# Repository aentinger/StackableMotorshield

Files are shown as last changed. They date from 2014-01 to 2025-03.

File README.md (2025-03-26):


💾 Stackable Motorshield
========================



# 📸 Image

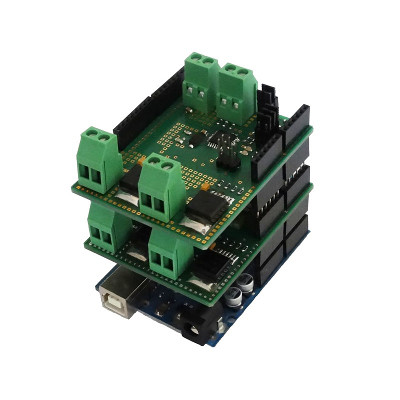
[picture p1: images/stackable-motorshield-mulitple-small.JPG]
LXRobotics P2 StackableMotorshield


# 📂 Description

The Stackable Motorshield facilitates the control of up to 8 high power motors (18 V / 46 A) using only one Arduino Board. This can be achived by using the same amount of Stackable Motorshields as the amount of motors desired to be controlled. The communication between Motorshields and Arduino Board is done over the I2C-Interface. The address of each Stackable Motorshields can be configured. Inputs for connecting rotary encoders for determining the number of rotations of the motor are available on the shield. For a quick and easy start, a open source Arduino library with sample programs is available.

**Features**

* Control of up to 8 High Power Motors through stacking of up to 8 Stackable Motorshields on top of each other
* Voltage supply range: 7 to 18 Volts
* Can be used with 2S, 3S and 4S LiPo-battery
* High performance: Maximum continuous output 46 A
* Control via I2C -  only 2 Arduino-Pins are required (SDA = A4, SCL = A5)
* I2C-PullUp-resistors connectable through jumper
* Adjustable address through jumper
* Inputs for rotary encoders
* Motor drivers are protected against short circuit (to ground/supply), overheating, overvoltage and undervoltage
* Arduino Library with example programs is available on GitHub
* 2 Status-LEDs (Orange: User LED, Red: Active when speed of motor > 0)

# 🎥 [Video](images/stackable_motorshield_demo.mp4)

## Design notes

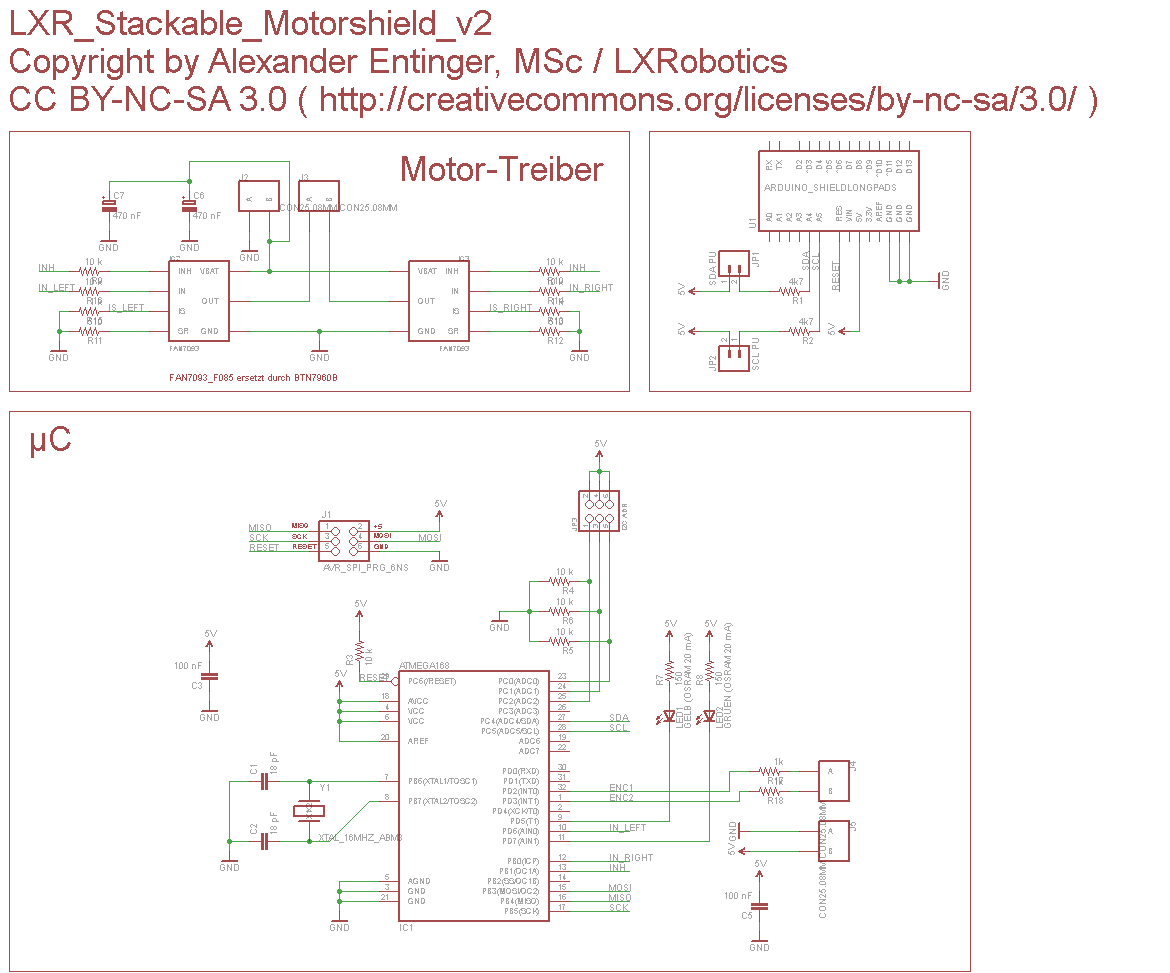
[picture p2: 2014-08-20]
hardware/lxr_stackable_motorshield_v2.png

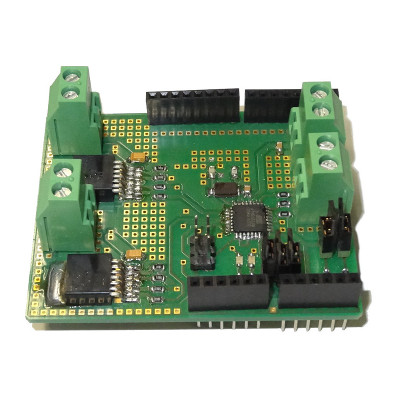
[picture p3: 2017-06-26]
images/stackable-motorshield-side-small.JPG

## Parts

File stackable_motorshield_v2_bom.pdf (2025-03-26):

Menge | Schaltplan | Bezeichnung | Farnell Bestell Nummer | Preis (1 Stück) | Gesamtpreis | Wird bestückt | Footprint | Säckchen
4 | J2, J3, J4, J5 | Schraubklemme 2 Polig | 3041165 | € 1,12 | € 4,48 | | | S1
2 | IC2, IC3 | FAN7093 Leistungshalbbrücke | 2290282 | € | 6,99 | € | 13,98 | x | Bei Farnell aus dem Sortiment genommen, Ersatztyp ist BTN7960B, Digikey-Bauteil-Bezeichnung BTN7960BCT-ND
2 | C6, C7 | KEMET Bauform A, 25 V, 470 nF, Tantal Ko | 1457425 | € | 0,15 | € | 0,30 | x | http://www.digikey.at/product-detail/de/BTN7960B/BTN7960BCT-ND/2231075
2 | C3, C5 | 100 nF, 100 V, 0805, Keramikkondensator | 1759144 | € 0,01 | € 0,02 | x
2 | C1, C2 | 18 pF, 100 V, 0805, Keramikkondensator | 1759194 | € 0,01 | € 0,03 | x
1 | Y1 | Quarz, 16 MHz, SMD | 1611806 | € 1,74 | € 1,74 | x
2 | R1, R2 | 4k7, 0805, Widerstand SMD | 1469923 | € 0,02 | € 0,04 | x
2 | R7, R8 | 150R, 0805, Widerstand SMD | 9333916 | € 0,01 | € 0,02 | x
4 | R13, R15, R17, R18 | 1k, 0805, Widerstand SMD | 1469847 | € 0,02 | € 0,09 | x
8 | R3, R4, R5, R6, R9, R10, R14, R16 | 10k, 0805, Widerstand SMD | 1469856 | € 0,02 | € 0,18 | x
2 | R11, R12 | 510R, 0805, Widerstand SMD | 1653016 | € 0,10 | € 0,20 | x
1 | IC1 | ATMega168, 32TQFP | 1841603 | € 2,79 | € 2,79 | x
2 | J1, JP3 | Stiftleiste, 2 x 3, 2.54 mm, Vertikal, Durchsteck | 1022226 | € 0,35 | € 0,70 | | S2
2 | JP1, JP2 | Stiftleiste, 1 x 2, 2.54 mm, Vertikal, Durchsteck | 3418285 | € 0,24 | € 0,48 | | S2
1 | LED1 | DIALIGHT, CHIPLED, 0805, Gelb, 2V, 20 mA, LY R976 | 1465993 | € 0,17 | € 0,17 | x
1 | LED2 | KINGBRIGHT, CHIPLED, 0805, Rot, 2V, 20 mA, LS R976 | 1686066 | € 0,17 | € 0,17 | x
1 | Arduino Stiftleistenset (Stecker lang) | ELV | € | 0,75 | € | 0,75 | S2 | http://www.elv.at/buchsenleisten-set-fuer-arduino-boards.html
5 | Jumper, 2.54 mm, 2 Polig | 4218176 | € | 0,14 | € | 0,68 | S3
| | | Summe | | € | 26,82

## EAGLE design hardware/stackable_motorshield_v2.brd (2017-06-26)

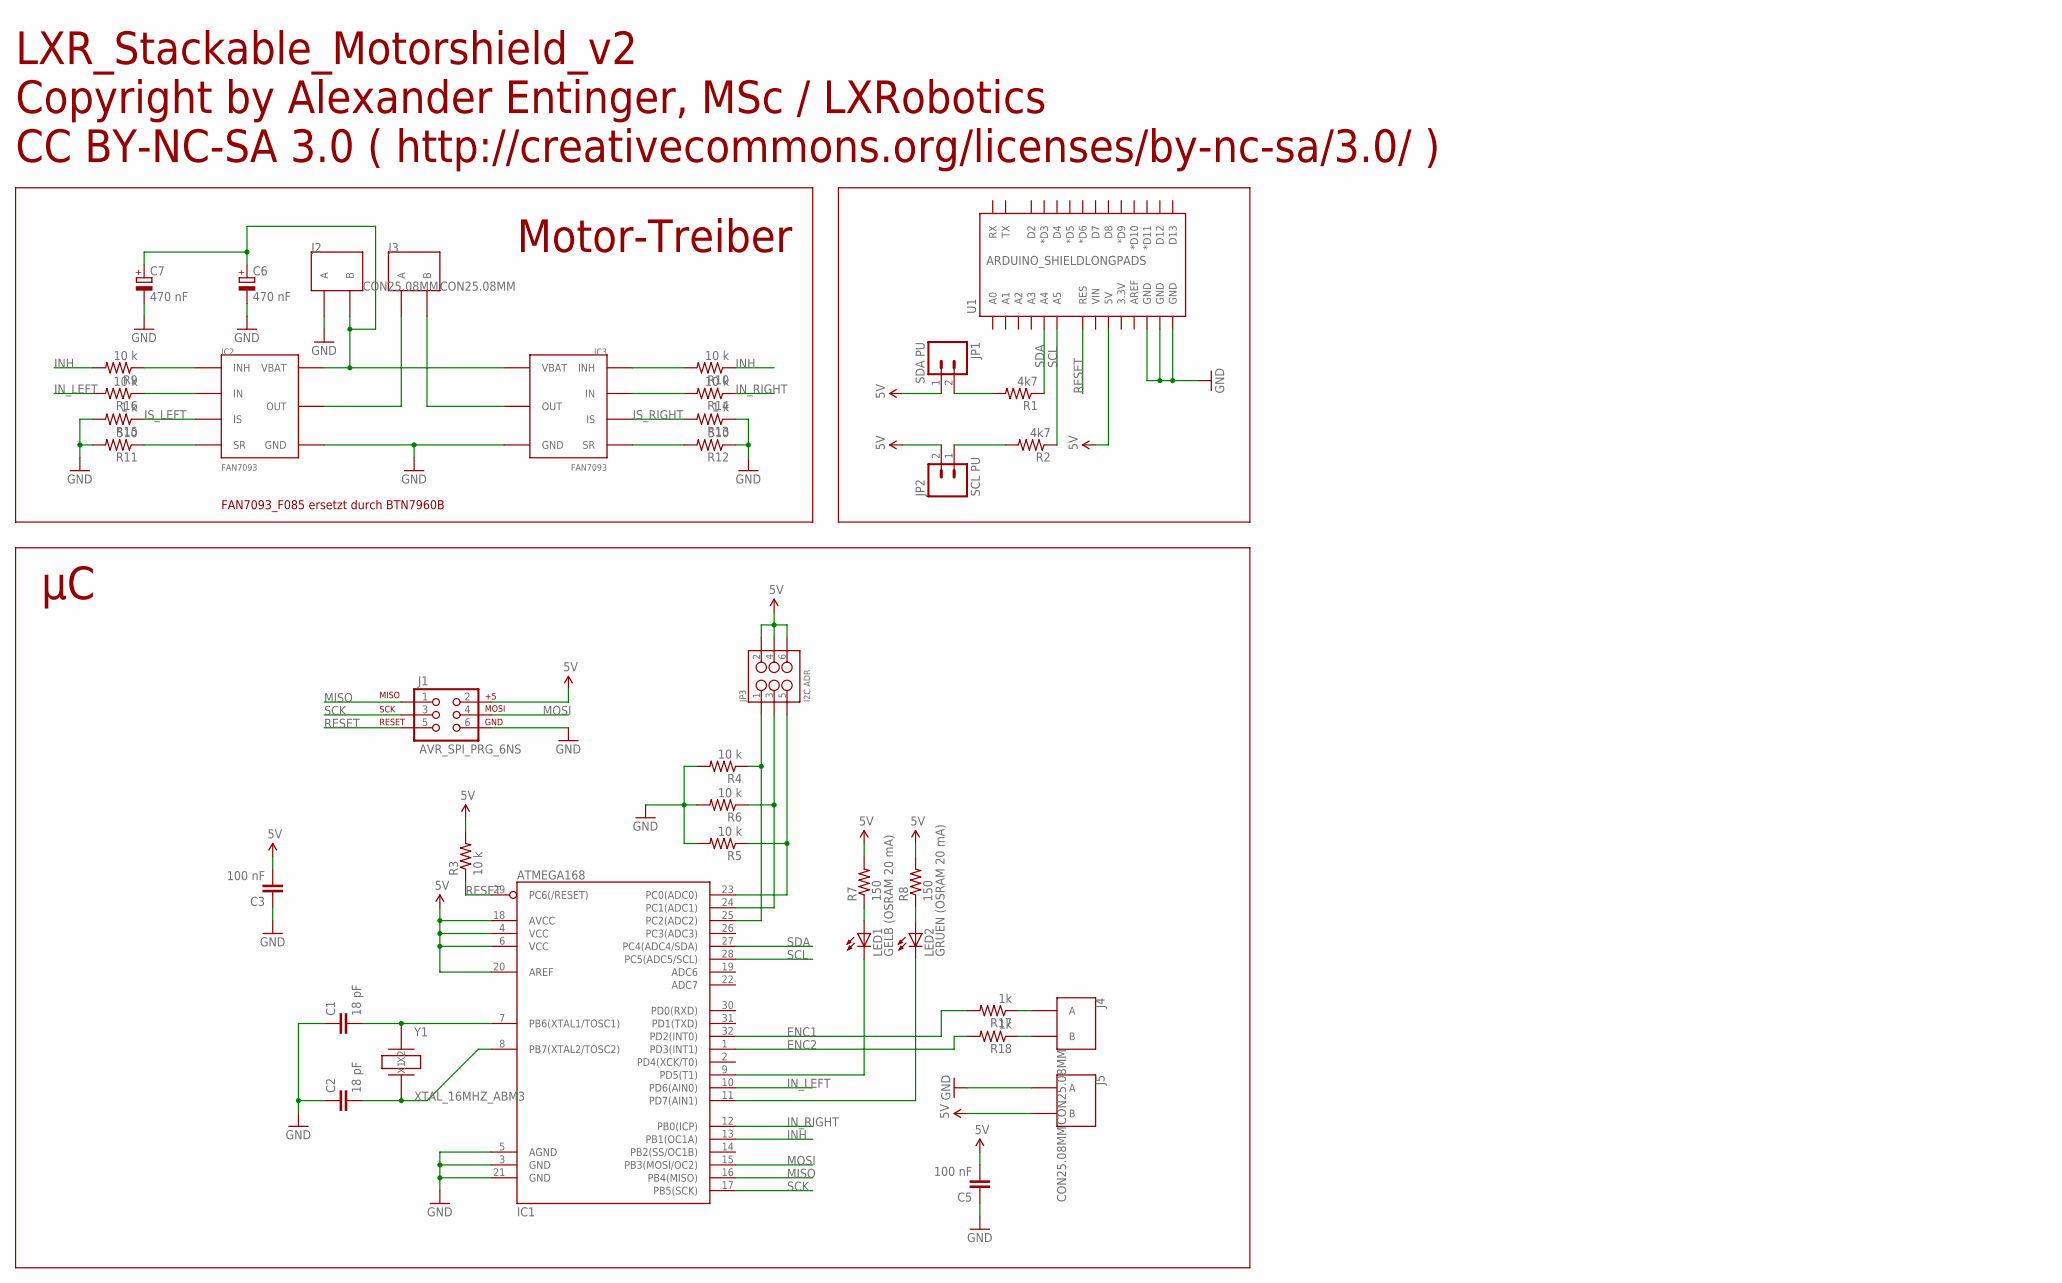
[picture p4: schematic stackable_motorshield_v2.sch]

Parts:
C1, C2: 18 pF; C0805
C3, C5: 100 nF; C0805
C6, C7: 470 nF; KEMET_A
IC1: ATMEGA168; TQFP32-08
IC2, IC3: FAN7093; TO263-7L
J1: AVR_SPI_PRG_6NS; 2X3-NS
J2, J3, J4, J5: CON25.08MM; CON2_SCHRAUBKLEMME
JP1: SDA PU; 1X02
JP2: SCL PU; 1X02
JP3: I2C ADR; 2X3_POGO
LED1: GELB (OSRAM 20 mA); CHIP-LED0805
LED2: GRUEN (OSRAM 20 mA); CHIP-LED0805
R1, R2: 4k7; 0805
R3, R4, R5, R6, R9, R10, R14, R16: 10 k; 0805
R7, R8: 150; 0805
R11, R12: 510; 0805
R13, R15: 1 k; 0805
R17, R18: 1k; 0805
U1: ARDUINO_SHIELDLONGPADS; DUEMILANOVE_SHIELD_LONGPADS
Y1: XTAL_16MHZ_ABM3; ABM3

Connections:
5V: C3.2, C5.2, IC1.4 (VCC), IC1.6 (VCC), IC1.18 (AVCC), IC1.20 (AREF), J1.2, J5.2 (B), JP1.1, JP2.2, JP3.P$2 (2), JP3.P$4 (4), JP3.P$6 (6), R3.2, R7.2, R8.2, U1.5V
ENC1: IC1.32 (PD2(INT0)), R17.2
ENC2: IC1.1 (PD3(INT1)), R18.2
GND: C1.1, C2.1, C3.1, C5.1, C6.CATHODE (-), C7.CATHODE (-), IC1.3 (GND), IC1.5 (AGND), IC1.21 (GND), IC2.GND, IC3.GND, J1.6, J2.1 (A), J5.1 (A), R4.2, R5.2, R6.2, R11.2, R12.1, R13.1, R15.2, U1.GND@0 (GND), U1.GND@1 (GND), U1.GND@2 (GND)
INH: IC1.13 (PB1(OC1A)), R9.2, R10.1
IN_LEFT: IC1.10 (PD6(AIN0)), R16.2
IN_RIGHT: IC1.12 (PB0(ICP)), R14.1
IS_LEFT: IC2.IS, R15.1
IS_RIGHT: IC3.IS, R13.2
MISO: IC1.16 (PB4(MISO)), J1.1
MOSI: IC1.15 (PB3(MOSI/OC2)), J1.4
unnamed: C1.2, IC1.7 (PB6(XTAL1/TOSC1)), Y1.X1
unnamed: C2.2, IC1.8 (PB7(XTAL2/TOSC2)), Y1.X2
unnamed: JP2.1, R2.2
unnamed: JP1.2, R1.2
unnamed: IC1.25 (PC2(ADC2)), JP3.P$1 (1), R4.1
unnamed: IC1.24 (PC1(ADC1)), JP3.P$3 (3), R6.1
unnamed: IC1.23 (PC0(ADC0)), JP3.P$5 (5), R5.1
unnamed: IC1.9 (PD5(T1)), LED1.C
unnamed: IC1.11 (PD7(AIN1)), LED2.C
unnamed: LED2.A, R8.1
unnamed: LED1.A, R7.1
unnamed: IC2.SR, R11.1
unnamed: IC3.SR, R12.2
unnamed: IC2.OUT, IC2.OUT@1 (OUT), J3.1 (A)
unnamed: IC2.INH, R9.1
unnamed: IC3.OUT, IC3.OUT@1 (OUT), J3.2 (B)
unnamed: C6.ANODE (+), C7.ANODE (+), IC2.VBATT (VBAT), IC3.VBATT (VBAT), J2.2 (B)
unnamed: J4.1 (A), R17.1
unnamed: IC3.INH, R10.2
unnamed: J4.2 (B), R18.1
unnamed: IC2.IN, R16.1
unnamed: IC3.IN, R14.2
RESET: IC1.29 (PC6(/RESET)), J1.5, R3.1, U1.RES
SCK: IC1.17 (PB5(SCK)), J1.3
SCL: IC1.28 (PC5(ADC5/SCL)), R2.1, U1.A5
SDA: IC1.27 (PC4(ADC4/SDA)), R1.1, U1.A4

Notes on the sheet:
LXR_Stackable_Motorshield_v2 Copyright by Alexander Entinger, MSc / LXRobotics CC BY-NC-SA 3.0 ( http://creativecommons.org/licenses/by-nc-sa/3.0/ )
Motor-Treiber
FAN7093_F085 ersetzt durch BTN7960B

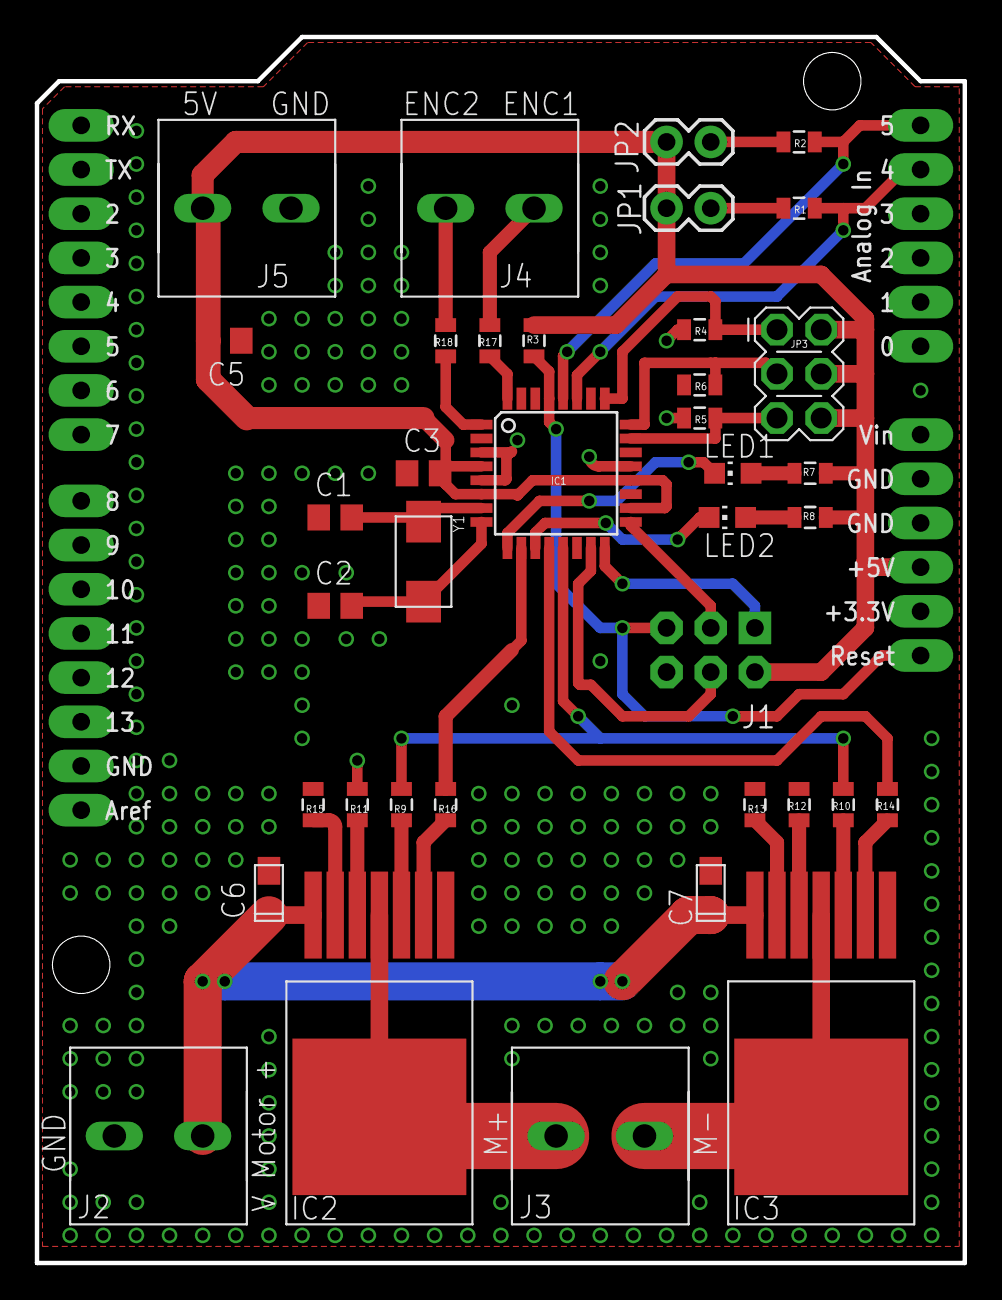
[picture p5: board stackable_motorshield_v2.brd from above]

Board: 2 copper layers, 53.3 x 70.5 mm, 39 parts (0 on the bottom side), 37 nets.

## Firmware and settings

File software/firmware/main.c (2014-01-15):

/**
* @author Alexander Entinger, MSc
* @brief main file for the stackable motor driver firmware
* @file main.c
* @license Attribution-NonCommercial-ShareAlike 3.0 Unported (CC BY-NC-SA 3.0) ( http://creativecommons.org/licenses/by-nc-sa/3.0/ )
*/

#include <avr/interrupt.h>
#include "motor_control.h"
#include "encoder.h"
#include "status_led_control.h"
#include "i2c.h"

/* PROTOTYPE SECTION */
void init_application();

int main(void) {
	
	init_application();
	
	for(;;) { // main working loop
		// loop forever	
	}
}

/**
 * @brief initializes the required peripherals
 */
void init_application() {
	
	init_motor_control();
	
	init_encoder();
	
	init_status_led_control();
	
	init_i2c();
		
	sei();
}

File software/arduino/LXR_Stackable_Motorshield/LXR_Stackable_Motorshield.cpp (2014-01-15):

/**
 * @author Alexander Entinger, MSc / LXRobotics
 * @brief this module implements the library for controlling the LXRobotics Stackable Motorshield
 * @file LXR_Stackable_Motorshield.cpp
 * @license Attribution-NonCommercial-ShareAlike 3.0 Unported (CC BY-NC-SA 3.0) ( http://creativecommons.org/licenses/by-nc-sa/3.0/ )
 */
 
#include "LXR_Stackable_Motorshield.h"
#include <Wire.h>

static uint8_t const CONTROL_STATUS_REG_ADR = 0;
static uint8_t const SPEED_REG_ADR = 1;
static uint8_t const ENCODER_1_LOW_REG_ADR = 2;
static uint8_t const ENCODER_2_LOW_REG_ADR = 4;
 
/**
 * @brief Constructor
 * @param dev_address stackable motorshield device address
 */
LXR_Stackable_Motorshield::LXR_Stackable_Motorshield(uint8_t const dev_address) : m_dev_address(dev_address) {
	Wire.begin();
}

/** 
 * @brief this function sets the speed of the motor
 * @param speed sets the speed of the motor (0 => stop(break), 200 => full speed)
 */
void LXR_Stackable_Motorshield::set_speed(uint8_t const speed) {
	Wire.beginTransmission(m_dev_address);
	Wire.write(SPEED_REG_ADR);
	Wire.write(speed);
	Wire.endTransmission();
}

/**
 * @brief reads the current speed
 */
int LXR_Stackable_Motorshield::get_speed() {
	Wire.beginTransmission(m_dev_address);
	Wire.write(SPEED_REG_ADR);
	Wire.endTransmission();
	delay(1);
	Wire.requestFrom(m_dev_address, (uint8_t)(2));
	return (int)(Wire.read());
}

/** 
 * @brief this function sets direction of the motor
 * @param dir direction of the motor (FWD, BWD)
 */
void LXR_Stackable_Motorshield::set_direction(E_DIRECTION const dir) {
	Wire.beginTransmission(m_dev_address);
	Wire.write(CONTROL_STATUS_REG_ADR);
	uint8_t data = 0x00;
    if(dir == FWD) data = 0x01;
	else if(dir == BWD) data = 0x02;
    Wire.write(data);
	Wire.endTransmission();
}

/**
 * @brief returns the current motor direction
 */
E_DIRECTION LXR_Stackable_Motorshield::get_direction() {
	Wire.beginTransmission(m_dev_address);
	Wire.write(CONTROL_STATUS_REG_ADR);
	Wire.endTransmission();
	delay(1);
	Wire.requestFrom(m_dev_address, (uint8_t)(2));
	uint8_t const reg_content = Wire.read();
	E_DIRECTION dir = BWD;
	if(reg_content & 0x01) dir = FWD;
	return dir;
}

/**
 * @brief enables the encoders
 */
void LXR_Stackable_Motorshield::enable_encoder() {
	Wire.beginTransmission(m_dev_address);
	Wire.write(CONTROL_STATUS_REG_ADR);
	uint8_t data = 0x04;
    Wire.write(data);
	Wire.endTransmission();
}
	
/**
 * @brief disables the encoders
 */
void LXR_Stackable_Motorshield::disable_encoder() {
	Wire.beginTransmission(m_dev_address);
	Wire.write(CONTROL_STATUS_REG_ADR);
	uint8_t data = 0x08;
    Wire.write(data);
	Wire.endTransmission();
}

/**
 * @brief returns true when the encoders are enabled, false otherwise
 */
bool LXR_Stackable_Motorshield::encoder_enabled() {
	Wire.beginTransmission(m_dev_address);
	Wire.write(CONTROL_STATUS_REG_ADR);
	Wire.endTransmission();
	delay(1);
	Wire.requestFrom(m_dev_address, (uint8_t)(2));
	uint8_t const reg_content = Wire.read();
	return (reg_content & 0x02);
}

/**
 * @brief read the encoder ticks measured at encoder 1 and reset the encoder counter in the process
 */
int LXR_Stackable_Motorshield::read_encoder_1() {
	Wire.beginTransmission(m_dev_address);
	Wire.write(ENCODER_1_LOW_REG_ADR);
	Wire.endTransmission();
	delay(1);
	Wire.requestFrom(m_dev_address, (uint8_t)(2));
	int const low_byte = (int)(Wire.read());
	int const high_byte = (int)(Wire.read());
	return ((high_byte<<8) + low_byte);
}
	
/**
 * @brief read the encoder ticks measured at encoder 1 and reset the encoder counter in the process
 */
int LXR_Stackable_Motorshield::read_encoder_2() {
	Wire.beginTransmission(m_dev_address);
	Wire.write(ENCODER_2_LOW_REG_ADR);
	Wire.endTransmission();
	delay(1);
	Wire.requestFrom(m_dev_address, (uint8_t)(2));
	int const low_byte = (int)(Wire.read());
	int const high_byte = (int)(Wire.read());
	return ((high_byte<<8) + low_byte);
}

/**
 * @brief turns the orange led on
 */
void LXR_Stackable_Motorshield::turn_orange_led_on() {
	Wire.beginTransmission(m_dev_address);
	Wire.write(CONTROL_STATUS_REG_ADR);
	uint8_t data = 0x10;
    Wire.write(data);
	Wire.endTransmission();
}
	
/**
 * @brief turns the orange led off
 */
void LXR_Stackable_Motorshield::turn_orange_led_off() {
	Wire.beginTransmission(m_dev_address);
	Wire.write(CONTROL_STATUS_REG_ADR);
	uint8_t data = 0x20;
    Wire.write(data);
	Wire.endTransmission();
}

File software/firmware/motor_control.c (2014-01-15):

/**
* @author Alexander Entinger, MSc
* @brief this module is responsible for controlling the motor via the half bridge
* @file motor_control.c
* @license Attribution-NonCommercial-ShareAlike 3.0 Unported (CC BY-NC-SA 3.0) ( http://creativecommons.org/licenses/by-nc-sa/3.0/ )
*/

#include "motor_control.h"
#include "hal.h"
#include <avr/interrupt.h>
#include <stdbool.h>

typedef struct {
	E_DIRECTION direction;
	uint8_t speed;
} s_motor_params;
static volatile s_motor_params motor_params = {FWD, 0};

/**
 * @brief initializes motor control
 */
void init_motor_control() {
	INLEFT_PORT &= ~(1<<INLEFT); // and there value to zero which leads to both halfbridges activate their low side switch only (break)
	INLEFT_DDR |= (1<<INLEFT); // set both inleft and inright to output ports
	INRIGHT_PORT &= ~(1<<INRIGHT);
	INRIGHT_DDR |= (1<<INRIGHT); 
	
	INH_PORT |= (1<<INH); // set /INH to output and high
	INH_DDR |= (1<<INH); // thus activating the half bridge
	
	TCNT0 = 0; // reset the tcnt register
	TIMSK0 |= (1<<TOIE0); // enable timer 0 overflow interrupt
	TCCR0B |= (1<<CS01); // prescaler = 8 => 1 Timerstep @ 16 MHz = 500 ns, 200 Timersteps = 100 us => 10 kHz PWM Frequency	
}

/** 
 * @brief this function sets direction of the motor
 * @param dir direction of the motor (FWD, BWD)
 */
void set_motor_direction(E_DIRECTION const dir) {
	motor_params.direction = dir;
}

/** 
 * @brief returns the current motor direction
 */
E_DIRECTION get_motor_direction() {
	return motor_params.direction;
}

/** 
 * @brief this function sets the speed of the motor
 * @param speed sets the speed of the motor (0 => stop(break), 200 => full speed)
 */
void set_motor_speed(uint8_t const speed) {	
	if(speed > MAX_MOTOR_SPEED) motor_params.speed = MAX_MOTOR_SPEED;
	else motor_params.speed = speed;
}

/** 
 * @brief returns the current motor speed
 */
uint8_t get_motor_speed() {
	return motor_params.speed;
}

/** 
 * @brief Timer 0 ISR
 */
ISR(TIMER0_OVF_vect) {
	static bool halfbridge_highside_active = false;
	
	if(motor_params.speed > 0) {

		/* ACTIVATE LOWSIDE DEPENDING ON THE DIRECTION */
		if(motor_params.direction == FWD) {
			INRIGHT_PORT &= ~(1<<INRIGHT); // lowside of right half bridge is constantly activated
		} else if(motor_params.direction == BWD) {
			INLEFT_PORT &= ~(1<<INLEFT); // lowside of left half bridge is constantly activated
		}

		/* TOOGLE HIGHSIDE DEPENDING ON THE DIRECTION */
		if(halfbridge_highside_active) {
			if(motor_params.direction == FWD) INLEFT_PORT |= (1<<INLEFT); // activate highside
			else if(motor_params.direction == BWD) INRIGHT_PORT |= (1<<INRIGHT); // activate highside
			halfbridge_highside_active = false;
			TCNT0 = 0xFF - motor_params.speed;
			} else {
			if(motor_params.direction == FWD) INLEFT_PORT &= ~(1<<INLEFT); // deactivate highside
			else if(motor_params.direction == BWD) INRIGHT_PORT &= ~(1<<INRIGHT); // deactivate highside
			halfbridge_highside_active = true;
			TCNT0 = 0xFF - (MAX_MOTOR_SPEED - motor_params.speed);
		}

	} else {
		INLEFT_PORT &= ~(1<<INLEFT);
		INRIGHT_PORT &= ~(1<<INRIGHT);	
	}
}

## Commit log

2014-01-15 initial checkin of stackable motorshield
2014-08-20 adding new schematic - FAN7093 replaced with BTN7960B
2014-10-31 adding binary for stackable motorshield onboard µC
2017-06-26 Adding hardware files + images
    [stackable_motorshield_v2.brd, stackable_motorshield_v2.sch]
2025-03-26 Add BOM.

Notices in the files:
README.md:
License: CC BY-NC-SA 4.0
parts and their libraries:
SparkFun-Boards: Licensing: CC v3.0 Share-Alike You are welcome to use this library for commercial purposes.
